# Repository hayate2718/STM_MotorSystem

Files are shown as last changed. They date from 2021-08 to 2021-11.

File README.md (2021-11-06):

# STM_MotorSystem
モーターシステム<br>
MCU_bord_subは半導体不足でMCP2562のSOIC8pinパッケージがなかったとき用<br>
VL逆接したら多分壊れるので気を付けてね。ダイオードつけるの忘れてたてへぺろリン<br>
ファームウェアなどプログラム関係は[STM_MotorSystem_Programのwiki](https://github.com/hayate2718/STM_MotorSystem_Program/wiki)を参照

|ピン|ペリフェラル|用途|
|---|---|---|
|PA0|TIM2(エンコーダモード)|直行エンコーダB相|
|PA1|TIM2(エンコーダモード)|直行エンコーダA相|
|PA2|GPIO(INPUT)|FF1|
|PA3|GPIO(INPUT)|FF2|
|PA5|ADC2|電流センサ出力|
|PA7|GPIO(OUTPUT)|RESET|
|PB0|TIM3(PWM)|モータ制御用PWM|
|PB1|GPIO(INPUT)|基板アドレス用ID1bit|
|PA8|GPIO(INPUT)|基板アドレス用ID2bit|
|PA9|GPIO(INPUT)|基板アドレス用ID3bit|
|PA10|GPIO(INPUT)|基板アドレス用ID4bit|
|PA11|CAN_RX|CAN_RX|
|PA12|CAN_TX|CAN_TX|
|PB4|GPIO(OUTPUT)|DIR|
|PB5|GPIO(OUTPUT)|COAST|

## 結局スナバ回路つけなかった

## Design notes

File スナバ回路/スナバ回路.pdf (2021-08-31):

# モータシステム：スナバ回路設計データ

### 小野澤颯

2021 年 8 月 30 日

## 1 目次

1. スナバ回路について
2. 非放電型スナバ回路の計算
3. モータシステム FET ブリッジへの実装
4. 参考文献

## 2 本編

1. スナバ回路について
MOSFET は非常に高速でスイッチングされるため、ドレイン電流は非常に急な変化をする。 例えば、モータ制御回路の H ブリッジ部に注目し、ハイサイド FET がターンオンしていると きモータに電流 I が流れる。次にターンオフしたとき、配線の寄生インダクタンス Lparasitic、 モータのインダクタンス成分 Lm によって、ドレインソース間には (Lparasitic + Lm)

dI
dt に従い、
大きなサージ電圧が発生する。このサージ電圧が FET の Vds(max) を超えると破壊される。

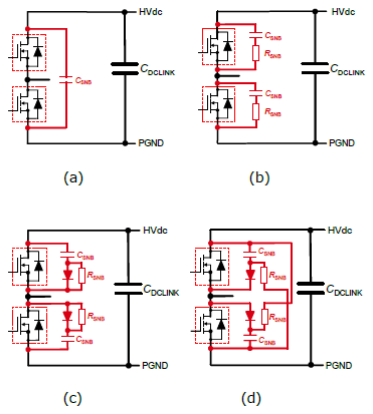
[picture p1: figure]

図 1: 各種スナバ回路

スナバ回路は破壊原因となる寄生成分によるサージを吸収し、FET の過渡電圧保護をする保 護回路の一種である。スナバ回路には大きく 4 種類あり、まず図１.(a) の C スナバ回路、次に 図 1.(b) に示す RC スナバ回路、図 1.(c) の RCD スナバ回路、図 1.(d) の非放電型 RCD スナバ 回路である。ここでは、非放電型 RCD スナバ回路を取り扱う。
非放電型 RCD スナバ回路は各種スナバ回路の中でもっともサージ吸収効果を高めることが 可能であり、スナバコンデンサがスイッチング毎に放電されないため、スナバ抵抗の消費電力 はサージによる電力のみとなる。したがって、スナバコンデンサの値を大きくすることができ るため、サージ吸収効果を大きく高めることが可能となる。他のスナバ回路ではスナバコンデ ンサがスイッチング毎に放電し、スナバ抵抗で電力を消費するため、スイッチング周波数が大 きくなると抵抗の消費電力が増大し、スナバコンデンサの大きさが制限される。他に比べ、非 放電型スナバ回路はメリットが多いが、もっとも配線レイアウトが複雑になるため、層の少な い基板では実装するのが困難である。
2. 非放電型 RCD スナバ回路の計算
非放電型 RCD スナバ回路の設計方法を示します。寄生インダクタンスにたまったエネルギー をスナバコンデンサで吸収することでサージを吸収しているため、スナバコンデンサは

Csnb >

LparasiticI

2

(Vds(surge) − Vsource)
2

(1)

で求める。これはインダクタンスのエネルギー式とコンデンサのエネルギー式から明らかであ る。
次に、吸収した電力の 90%を消費するスナバ抵抗の設計方法を示す。

Rsnb <

1

fswCsnb2.3

(2)

この抵抗器は、小さすぎると発振する可能性があるためできるだけ用件満たす範囲で多き値 を使う。
上式の求め方を下記に簡単に示す。前提として、Vc = Vsource(1 − e

− t
rc ) は RC 直列回路のコ
ンデンサ電位の t 軸関数である。

Vc(snb) = Vds(surge)(1 − e

− | t
RsnbCsnb ) | (3)

t はスイッチング周期だから　 t =

1
fsw

Vc(snb) = Vds(surge)(1 − e

− | 1
fswRsnbCsnb ) | (4)

e

− 1
fswRsnbCsnb =

Vds(surge) − Vc(snb)

Vds(surge)

(5)
−

1

fswRsnbCsnb

= log[

Vds(surge) − Vc(snb)

Vds(surge)

] | (6)

Rsnb =

−1

fswCsnblog[

Vds(surge)−Vc(snb)

Vds(surge)

]

(7)

コンデンサ電位を 90%消費するとき　 Vc(snb) = 0.9Vds(surge)

log[

Vds(surge) − 0.9Vds(surge)

Vds(surge)

] ≃ −2.3 | (8)

次に、スナバ抵抗の消費電力の設計方法を示す。

Psnb =

LparasiticI

2
fsw
2

(9)

これは、寄生インダクタンスのエネルギーがスイッチング毎に消費されていることを示して いる。

3. モータシステム FET ブリッジへの実装
用いるスナバ回路はまず、モータシステムで扱う最大電流 Imax、電源電圧 Vsource、FET の絶 対最大定格 Vmax、PWM 周波数 fsw を定義する。 例として、(あくまで例です（重要なことなので二回言います）)
Imax = 100[A] | (10)
Vsource = 24[V ] | (11)
Vmax = 30[V ] | (12)
fsw = 100[kHz] | (13)

と定義する。また、ここでは寄生インダクタンスを 100nH と定義する。
したがって、式 1 より、Csnb > 0.28[nF] となり、E 系列より 0.33[µF] を選択する。
式 2 より、Rsnb < 13[Ω] となるため、10[Ω] を選択する。
式 9 より、抵抗の損失は Psnb = 50[W] となるが、この電力は現実的ではないため、100A が 流れる時はモータの過渡電流と考え、約 0.1sec とし、半分の 5[W] 抵抗を用いる。（これでもで かいなぁ）
4. 参考文献
Rohm アプリケーションノート [スナバ回路の設計](62AN036J) (https://fscdn.rohm.com/jp/products/databook/applinote/discrete/sic/mosfet/sic-mos_snubber_circuit_design_an-j.pdf) 富士電機　アプリケーションノート [保護回路設計法] (https://www.fujielectric.co.jp/products/semiconductor/model/igbt/application/igbt.html)

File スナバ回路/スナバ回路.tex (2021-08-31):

\documentclass[12pt,a4paper,dvipdfmx]{jarticle}
\usepackage[top = 20truemm, bottom = 20truemm, left = 15truemm , right = 15truemm]{geometry}
\usepackage[dvipdfmx]{graphicx}
\usepackage{here}
\usepackage[dvipdfmx]{hyperref}
\usepackage{pxjahyper}
\hypersetup{
	bookmarksnumbered = true,
	colorlinks = true,
	setpagesize = false,
	linkcolor = blue,
	urlcolor = blue
}
\title{モータシステム：スナバ回路設計データ}
\author{小野澤颯}
\begin{document}
\maketitle
\section {目次}
\begin {enumerate}
	\item \hyperlink{section1}{スナバ回路について}
	\item \hyperlink{section2}{非放電型スナバ回路の計算}
	\item \hyperlink{section3}{モータシステムFETブリッジへの実装}
	\item \hyperlink{section4}{参考文献}
\end{enumerate}
\section {本編}
\begin{enumerate}
	\item \hypertarget{section1}{スナバ回路について}\\
		　MOSFETは非常に高速でスイッチングされるため、ドレイン電流は非常に急な変化をする。例えば、モータ制御回路のHブリッジ部に注目し、ハイサイドFETがターンオンしているときモータに電流$I$が流れる。次にターンオフしたとき、配線の寄生インダクタンス$L_{parasitic}$、モータのインダクタンス成分$L_{m}$によって、ドレインソース間には$(L_{parasitic}+L_{m})\frac{dI}{dt}$に従い、大きなサージ電圧が発生する。このサージ電圧がFETの$V_{ds(max)}$を超えると破壊される。\\
		\begin{figure}[H]
		\centering
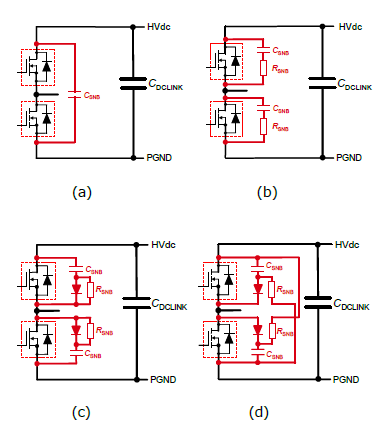
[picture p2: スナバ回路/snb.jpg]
		
		\caption{各種スナバ回路}
		\end{figure}
		　スナバ回路は破壊原因となる寄生成分によるサージを吸収し、FETの過渡電圧保護をする保護回路の一種である。スナバ回路には大きく4種類あり、まず図１.(a)のCスナバ回路、次に図1.(b)に示すRCスナバ回路、図1.(c)のRCDスナバ回路、図1.(d)の非放電型RCDスナバ回路である。ここでは、非放電型RCDスナバ回路を取り扱う。\\
		　非放電型RCDスナバ回路は各種スナバ回路の中でもっともサージ吸収効果を高めることが可能であり、スナバコンデンサがスイッチング毎に放電されないため、スナバ抵抗の消費電力はサージによる電力のみとなる。したがって、スナバコンデンサの値を大きくすることができるため、サージ吸収効果を大きく高めることが可能となる。他のスナバ回路ではスナバコンデンサがスイッチング毎に放電し、スナバ抵抗で電力を消費するため、スイッチング周波数が大きくなると抵抗の消費電力が増大し、スナバコンデンサの大きさが制限される。他に比べ、非放電型スナバ回路はメリットが多いが、もっとも配線レイアウトが複雑になるため、層の少ない基板では実装するのが困難である。
	\item \hypertarget{section2}{非放電型RCDスナバ回路の計算}\\
		 　非放電型RCDスナバ回路の設計方法を示します。寄生インダクタンスにたまったエネルギーをスナバコンデンサで吸収することでサージを吸収しているため、スナバコンデンサは
		 \begin{equation}
		 \label{csnb}
		 C_{snb}>\frac{L_{parasitic}I^2}{(V_{ds(surge)}-V_{source})^2}
		 \end{equation}
		で求める。これはインダクタンスのエネルギー式とコンデンサのエネルギー式から明らかである。\\
		　次に、吸収した電力の90\%を消費するスナバ抵抗の設計方法を示す。
		\begin{equation}
		\label{rsnb}
		R_{snb}<\frac{1}{f_{sw}C_{snb}2.3}
		\end{equation}
		　この抵抗器は、小さすぎると発振する可能性があるためできるだけ用件満たす範囲で多き値を使う。\\
		　上式の求め方を下記に簡単に示す。前提として、$V_c=V_{source}(1-e^{-\frac{t}{rc}})$はRC直列回路のコンデンサ電位のt軸関数である。
		\begin{eqnarray}
		V_{c(snb)}=V_{ds(surge)}(1-e^{-\frac{t}{R_{snb}C_{snb}}})
		\end{eqnarray}
		tはスイッチング周期だから　$t=\frac{1}{f_{sw}}$
		\begin{eqnarray}
		V_{c(snb)}=V_{ds(surge)}(1-e^{-\frac{1}{f_{sw}R_{snb}C_{snb}}})\\
		e^{-\frac{1}{f_{sw}R_{snb}C_{snb}}}=\frac{V_{ds(surge)}-V_{c(snb)}}{V_{ds(surge)}}\\
		-\frac{1}{f_{sw}R_{snb}C_{snb}}=log[\frac{V_{ds(surge)}-V_{c(snb)}}{V_{ds(surge)}}
]\\
		R_{snb}=\frac{-1}{f_{sw}C_{snb}log[\frac{V_{ds(surge)}-V_{c(snb)}}{V_{ds(surge)}}
]}
		\end{eqnarray}
		コンデンサ電位を90\%消費するとき　$V_{c(snb)}=0.9V_{ds(surge)}$\\
		\begin{eqnarray}
		log[\frac{V_{ds(surge)}-0.9V_{ds(surge)}}{V_{ds(surge)}}]\simeq-2.3
		\end{eqnarray}
		　次に、スナバ抵抗の消費電力の設計方法を示す。\\
		\begin{equation}
		\label{psnb}
		P_{snb}=\frac{L_{parasitic}I^2f_sw}{2}
		\end{equation}
		　これは、寄生インダクタンスのエネルギーがスイッチング毎に消費されていることを示している。\\
	\item \hypertarget{section3}{モータシステムFETブリッジへの実装}\\
		　用いるスナバ回路はまず、モータシステムで扱う最大電流$I_{max}$、電源電圧$V_{source}$、FETの絶対最大定格$V_{max}$、PWM周波数$f_{sw}$を定義する。\\
		　例として、(あくまで例です（重要なことなので二回言います）)
		\begin{eqnarray}
			I_{max} = 100 [A]\\
			V_{source} = 24 [V]\\
			V_{max} = 30 [V]\\
			f_{sw} = 100 [kHz]
		\end{eqnarray}
		と定義する。また、ここでは寄生インダクタンスを$100nH$と定義する。\\
		　したがって、式\ref{csnb}より、$C_{snb}　> 0.28 [nF]$となり、E系列より$0.33[\mu F]$を選択する。\\
		 　式\ref{rsnb}より、$R_{snb} < 13 [\Omega]$となるため、$10 [\Omega]$を選択する。\\
		 　式\ref{psnb}より、抵抗の損失は$P_{snb} = 50[W]$となるが、この電力は現実的ではないため、100Aが流れる時はモータの過渡電流と考え、約0.1secとし、半分の$5[W]$抵抗を用いる。（これでもでかいなぁ）
	\item \hypertarget{section4}{参考文献}\\
		Rohm　\href{https://fscdn.rohm.com/jp/products/databook/applinote/discrete/sic/mosfet/sic-mos_snubber_circuit_design_an-j.pdf}{アプリケーションノート[スナバ回路の設計](62AN036J)}\\
		富士電機　\href{https://www.fujielectric.co.jp/products/semiconductor/model/igbt/application/igbt.html}{アプリケーションノート[保護回路設計法]}
		
\end{enumerate}

\end{document}

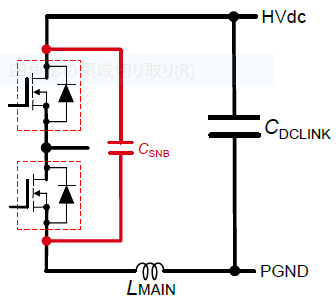
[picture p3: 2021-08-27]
スナバ回路/csnb.jpg

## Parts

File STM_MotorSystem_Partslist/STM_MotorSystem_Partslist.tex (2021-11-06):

\documentclass[12pt,a4paper,dvipdfmx]{jarticle}
\usepackage[top = 20truemm, bottom = 20truemm, left = 15truemm , right = 15truemm]{geometry}
\usepackage[dvipdfmx]{graphicx}
\usepackage{here}
\usepackage[dvipdfmx]{hyperref}
\usepackage{pxjahyper}
\hypersetup{
	bookmarksnumbered = true,
	colorlinks = true,
	setpagesize = false,
	linkcolor = blue,
	urlcolor = blue
}
\title{STMMotorSystemパーツリスト}
\author{小野澤颯}
\begin{document}
\maketitle
\begin{tabular}{ccccl}
	\hline
	部品名 &必要個数& 買う場所 & 金額 & 備考\\
	\hline
	XH8PIN &2& \href{hhttps://akizukidenshi.com/catalog/g/gC-12253/}{秋月電子} & 15 &コネクタ\\
	\hline
	XH5PIN$1$\href{https://akizukidenshi.com/catalog/g/gC-12250/}{秋月電子}$15$\\
	\hline
	JQ8PIN$2$\href{https://www.digikey.jp/product-detail/ja/jst-sales-america-inc/08JQ-BT/455-2970-ND/4918702}{digikey}$67$現在品切れ\\
	\hline
	VL4PIN&1&\href{https://www.digikey.jp/product-detail/ja/jst-sales-america-inc/B04P-VL-VN-1-8/455-3601-ND/2426345}{digikey}&156 &現在品切れ\\
	\hline
	box10pinL&1&\href{https://akizukidenshi.com/catalog/g/gC-13178/}{秋月電子}&25&ライトアングルタイプ\\
	\hline
	BOX14P$1$\href{https://www.digikey.jp/product-detail/ja/samtec-inc/FTSH-107-01-L-D-K/612-FTSH-107-01-L-D-K-ND/6693516}{digikey}$574$1.27ピッチ\\
	\hline
	TAKUTOSUITTI2$1$\href{https://akizukidenshi.com/catalog/g/gP-14888/}{秋月電子}$110$5個入り\\
	\hline
	DIPSW4$1$\href{https://akizukidenshi.com/catalog/g/gP-08929/}{秋月電子}$100$\\
	\hline
	ADP151AUJZ &1&\href{https://akizukidenshi.com/catalog/g/gI-14180/}{秋月電子}&90&\\
	\hline
	NJW1616T&1&\href{https://akizukidenshi.com/catalog/g/gI-15765/}{秋月電子}&90&\\
	\hline
	TLP291&1&\href{https://akizukidenshi.com/catalog/g/gI-16070/}{秋月電子}&180&10個入り\\
	\hline
	TLP293-4&1&\href{https://akizukidenshi.com/catalog/g/gI-16115/}{秋月電子}&80&\\
	\hline
	TLP152&1&\href{https://akizukidenshi.com/catalog/g/gI-10824/}{秋月電子}&80&\\
	\hline
	A3921&1&\href{https://akizukidenshi.com/catalog/g/gI-12293/}{秋月電子}&350&\\
	\hline
	ACS711&1&\href{https://akizukidenshi.com/catalog/g/gI-12267/}{秋月電子}&240&デフォではこいつ使おうとしてた\\
	\hline
	MCP2562$1$\href{https://www.digikey.jp/product-detail/ja/microchip-technology/MCP2562T-E-SN/MCP2562T-E-SNCT-ND/5011025}{digikey}$134$SOIC8PIN、現在在庫なし\\
	\hline
	STM32F303K$1$\href{https://akizukidenshi.com/catalog/g/gI-10790/}{秋月電子}$500$\\
	\hline
	SBR15U30SP5&4&\href{https://akizukidenshi.com/catalog/g/gI-07391/}{秋月電子}&50&\\
	\hline
	SS2040&1&\href{https://akizukidenshi.com/catalog/g/gI-02073/}{秋月電子}&300&20個入り\\
	\hline
	SKI03021&4&\href{https://akizukidenshi.com/catalog/g/gI-08473/}{秋月電子}&100&\\
	\hline
	FDC6305&2&\href{https://akizukidenshi.com/catalog/g/gI-06003/}{秋月電子}&120&10個入り\\
	\hline
	RGBLED&1&\href{https://akizukidenshi.com/catalog/g/gI-12726/}{秋月電子}&100&10個入り\\
	\hline
	0Ω&1& & &1608\\
	\hline
	1kΩ&5& & &1608\\
	\hline
	2.4kΩ&1& & &1608\\
	\hline
	20kΩ&1& & &1608\\
	\hline
	33kΩ&1& & &1608\\
	\hline
	10kΩ&7& & &1608\\
	\hline
	10Ω&5& & &1608\\
	\hline
	3.3kΩ&1& & &1608\\
	\hline
	2kΩ&1& & &1608\\
	\hline
	120Ω$1$$$1608\\
	\hline
	集合10k&2&\href{https://akizukidenshi.com/catalog/g/gP-04664/}{秋月電子}&100&1005、100個入り\\
	\hline
	集合1k&3&\href{https://www.mouser.jp/ProductDetail/667-EXB-38V102JV}{Mouser}&12&0603\\
	\hline
	330uF&3&\href{https://akizukidenshi.com/catalog/g/gP-14450/}{秋月電子}&80&\\
	\hline
	0.1uF&7& & &1608\\
	\hline
	1uF&2& & &1608\\
	\hline
	0.22uF&2& & &1608\\
	\hline
	10uF&1& & &1608\\
	\hline
	4.7uF&1& & &1608\\
	\hline
	2.2uF&2& & &1608\\
	\hline
	100uF&1& & &3216\\
	\hline
	22uH&1&\href{https://akizukidenshi.com/catalog/g/gP-08321/}{秋月電子}&60&\\
	\hline
	CSTN12MHz$1$\href{https://akizukidenshi.com/catalog/g/gP-14561/}{秋月電子}$110$5個入り、セラロック\\
	\hline
\end{tabular}

\end{document}

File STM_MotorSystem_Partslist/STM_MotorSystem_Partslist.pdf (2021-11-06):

# STMMotorSystemパーツリスト

## 小野澤颯

### 2021 年 11 月 6 日

1

部品名 | 必要個数 買う場所 金額 備考
XH8PIN | 2 | 秋月電子 | 15 | コネクタ
XH5PIN1 秋月電子 (https://akizukidenshi.com/catalog/g/gC-12250/) 15
JQ8PIN2digikey67 (https://www.digikey.jp/product-detail/ja/jst-sales-america-inc/08JQ-BT/455-2970-ND/4918702) 現在品切れ
VL4PIN | 1 | digikey (https://www.digikey.jp/product-detail/ja/jst-sales-america-inc/B04P-VL-VN-1-8/455-3601-ND/2426345) | 156 | 現在品切れ
box10pinL | 1 | 秋月電子 (https://akizukidenshi.com/catalog/g/gC-13178/) | 25 | ライトアングルタイプ
BOX14P1digikey5741.27 (https://www.digikey.jp/product-detail/ja/samtec-inc/FTSH-107-01-L-D-K/612-FTSH-107-01-L-D-K-ND/6693516) ピッチ
TAKUTOSUITTI21 秋月電子 (https://akizukidenshi.com/catalog/g/gP-14888/) 1105 個入り DIPSW41 秋月電子 (https://akizukidenshi.com/catalog/g/gP-08929/) 100
ADP151AUJZ | 1 | 秋月電子 (https://akizukidenshi.com/catalog/g/gI-14180/) | 90
NJW1616T | 1 | 秋月電子 (https://akizukidenshi.com/catalog/g/gI-15765/) | 90
TLP291 | 1 | 秋月電子 (https://akizukidenshi.com/catalog/g/gI-16070/) | 180 | 10 個入り
TLP293-4 | 1 | 秋月電子 (https://akizukidenshi.com/catalog/g/gI-16115/) | 80
TLP152 | 1 | 秋月電子 (https://akizukidenshi.com/catalog/g/gI-10824/) | 80
A3921 | 1 | 秋月電子 (https://akizukidenshi.com/catalog/g/gI-12293/) | 350
ACS711 | 1 | 秋月電子 (https://akizukidenshi.com/catalog/g/gI-12267/) | 240 | デフォではこいつ使おうとしてた
MCP25621digikey134SOIC8PIN、現在在庫なし (https://www.digikey.jp/product-detail/ja/microchip-technology/MCP2562T-E-SN/MCP2562T-E-SNCT-ND/5011025) STM32F303K1 秋月電子 (https://akizukidenshi.com/catalog/g/gI-10790/) 500
SBR15U30SP5 | 4 | 秋月電子 (https://akizukidenshi.com/catalog/g/gI-07391/) | 50
SS2040 | 1 | 秋月電子 (https://akizukidenshi.com/catalog/g/gI-02073/) | 300 | 20 個入り
SKI03021 | 4 | 秋月電子 (https://akizukidenshi.com/catalog/g/gI-08473/) | 100
FDC6305 | 2 | 秋月電子 (https://akizukidenshi.com/catalog/g/gI-06003/) | 120 | 10 個入り
RGBLED | 1 | 秋月電子 (https://akizukidenshi.com/catalog/g/gI-12726/) | 100 | 10 個入り
0 Ω | 1 | | | 1608
1k Ω | 5 | | | 1608
2.4k Ω | 1 | | | 1608
20k Ω | 1 | | | 1608
33k Ω | 1 | | | 1608
10k Ω | 7 | | | 1608
10 Ω | 5 | | | 1608
3.3k Ω | 1 | | | 1608
2k Ω | 1 | | | 1608
120 Ω 11608
集合 10k | 2 | 秋月電子 (https://akizukidenshi.com/catalog/g/gP-04664/) | 100 | 1005、100 個入り
集合 1k | 3 | Mouser (https://www.mouser.jp/ProductDetail/667-EXB-38V102JV) | 12 | 0603
330uF | 3 | 秋月電子 (https://akizukidenshi.com/catalog/g/gP-14450/) | 80
0.1uF | 7 | | | 1608
1uF | 2 | | | 1608
0.22uF | 2 | | | 1608
10uF | 1 | | | 1608
4.7uF | 1 | | | 1608
2.2uF | 2 | | | 1608
100uF | 1 | | | 3216
22uH | 1 | 秋月電子 (https://akizukidenshi.com/catalog/g/gP-08321/) | 60
CSTN12MHz1 秋月電子 (https://akizukidenshi.com/catalog/g/gP-14561/) 1105 個入り、セラロック2

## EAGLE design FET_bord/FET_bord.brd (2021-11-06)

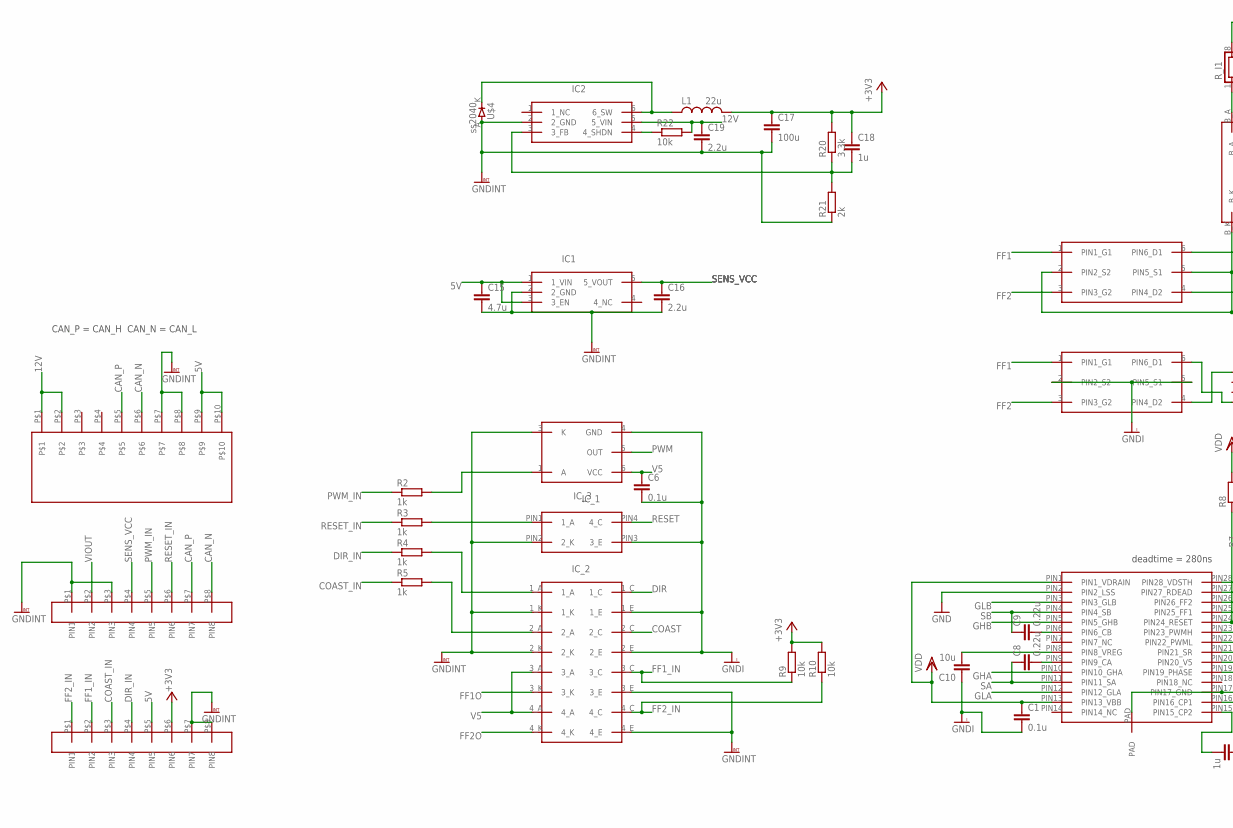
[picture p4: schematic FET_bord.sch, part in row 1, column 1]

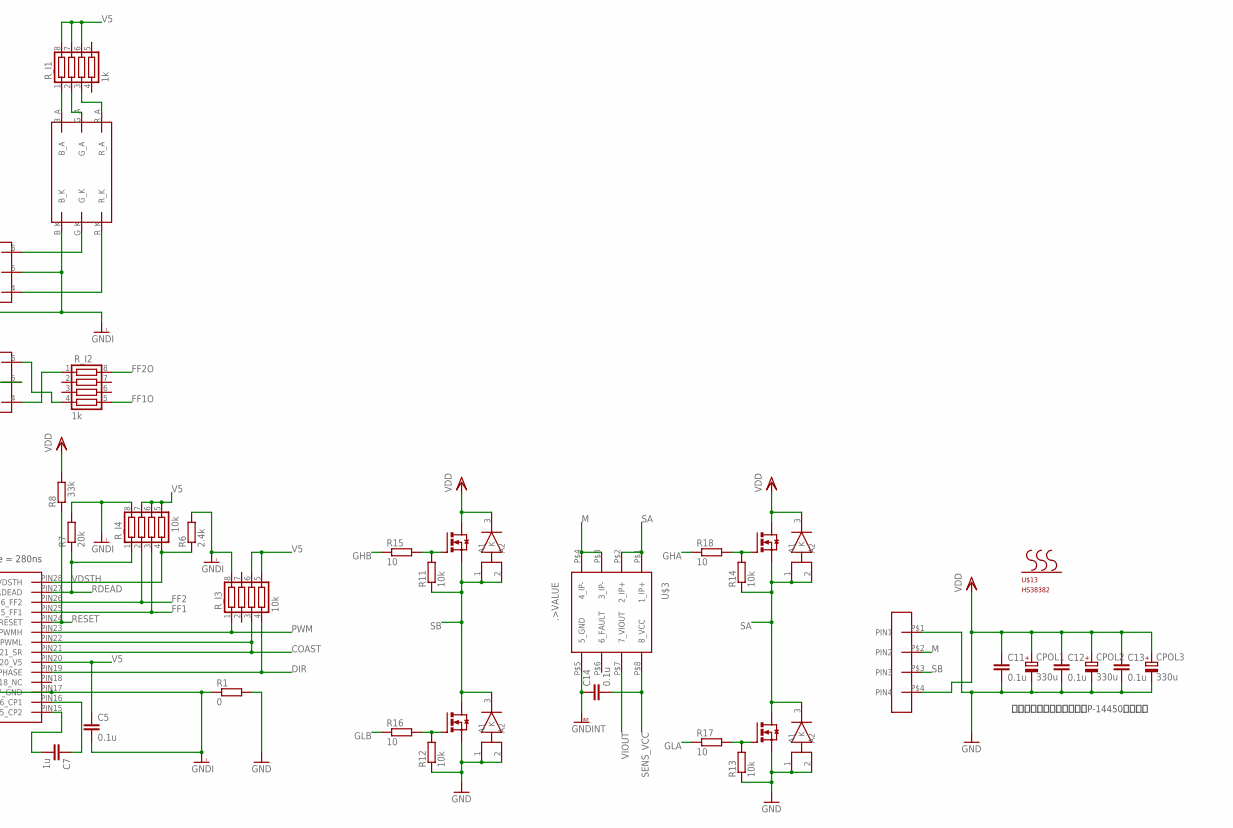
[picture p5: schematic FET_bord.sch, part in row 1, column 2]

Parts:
C1, C5, C6, C11, C12, C13, C14: 0.1u; C1608
C7, C18: 1u; C1608
C8, C9: 0.22u; C1608
C10: 10u; C1608
C15: 4.7u; C1608
C16, C19: 2.2u; C1608
C17: 100u; C3216
CON1, CON2: JQ_P8P
CPOL1, CPOL2, CPOL3: 330u; 1014CAPA
IC1: ADP151AUJZ; SOT23-5
IC2: NJW1616T; SOT23-6
IC_1: TLP291
IC_2: TLP290-4; TLP290
IC_3: TLP152; SO6-5
L1: 22u; SMD_INDUCTOR
R1: 0; 1608
R2, R3, R4, R5: 1k; 1608
R6: 2.4k; 1608
R7: 20k; 1608
R8: 33k; 1608
R9, R10, R11, R12, R13, R14, R22: 10k; 1608
R15, R16, R17, R18: 10; 1608
R20: 3.3k; 1608
R21: 2k; 1608
R_I1, R_I2: 1k; 0603X4RESISTOR
R_I3, R_I4: 10k; 1005X4RESISTOR
TR1, TR2, TR3, TR4: SKI03021; D2PACK
U$1: VL_4P
U$2: A3921; TSSOP_28P_ALLEGRO
U$3: ACS711; SOIC8
U$4: ss2040; SOD_123
U$5, U$7: FDC6305; SSOT6
U$6: RGB_LED
U$8: BOX10PBOX10P-L; BOX10P-L
U$9, U$10, U$11, U$12: SBR15U30SP5; POWERDI_5
U$13: HS38382; 38X38SQ

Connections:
5V: C15.1, CON1.P$5 (PIN5), IC1.1 (1_VIN), IC1.3 (3_EN), U$8.P$9, U$8.P$10
12V: C19.1, IC2.5 (5_VIN), R22.2, U$8.P$1, U$8.P$2
+3V3: C17.1, C18.1, CON1.P$6 (PIN6), L1.P$2 (2), R9.2, R10.2, R20.2
CAN_N: CON2.P$8 (PIN8), U$8.P$6
CAN_P: CON2.P$7 (PIN7), U$8.P$5
COAST: IC_2.2_C, R_I3.3, U$2.PIN21 (PIN21_SR), U$2.PIN22 (PIN22_PWML)
COAST_IN: CON1.P$3 (PIN3), R5.1
DIR: IC_2.1_C, R_I3.4, U$2.PIN19 (PIN19_PHASE)
DIR_IN: CON1.P$4 (PIN4), R4.1
FF1: R_I4.3, U$2.PIN25 (PIN25_FF1), U$5.1 (PIN1_G1), U$7.1 (PIN1_G1)
FF1O: IC_2.3_K, R_I2.5
FF1_IN: CON1.P$2 (PIN2), IC_2.3_C, R9.1
FF2: R_I4.2, U$2.PIN26 (PIN26_FF2), U$5.3 (PIN3_G2), U$7.3 (PIN3_G2)
FF2O: IC_2.4_K, R_I2.8
FF2_IN: CON1.P$1 (PIN1), IC_2.4_C, R10.1
GHA: R18.1, U$2.PIN10 (PIN10_GHA)
GHB: R15.1, U$2.PIN5 (PIN5_GHB)
GLA: R17.1, U$2.PIN12 (PIN12_GLA)
GLB: R16.1, U$2.PIN3 (PIN3_GLB)
GND: C11.2, C12.2, C13.2, CPOL1.-, CPOL2.-, CPOL3.-, R1.2, R12.1, R13.1, TR3.3 (PIN3_S), TR4.3 (PIN3_S), U$1.P$1 (PIN1), U$2.PIN2 (PIN2_LSS), U$10.1 (A1), U$10.2 (A2), U$11.1 (A1), U$11.2 (A2)
GNDI: C1.2, C5.2, C6.2, C10.1, IC_1.PIN3 (3_E), IC_2.1_E, IC_2.2_E, IC_3.4 (GND), R1.1, R6.2, R7.2, R_I3.8, R_I4.8, U$2.PAD, U$2.PIN17 (PIN17_GND), U$5.2 (PIN2_S2), U$5.5 (PIN5_S1), U$6.B_K, U$7.2 (PIN2_S2), U$7.5 (PIN5_S1)
GNDINT: C14.1, C15.2, C16.2, C17.2, C19.2, CON1.P$7 (PIN7), CON1.P$8 (PIN8), CON2.P$1 (PIN1), CON2.P$3 (PIN3), IC1.2 (2_GND), IC2.2 (2_GND), IC_1.PIN2 (2_K), IC_2.1_K, IC_2.2_K, IC_2.3_E, IC_2.4_E, IC_3.3 (K), R21.1, U$3.P$5 (5_GND), U$4.A, U$8.P$7, U$8.P$8
M: U$1.P$2 (PIN2), U$3.P$3 (3_IP-), U$3.P$4 (4_IP-)
unnamed: U$5.6 (PIN6_D1), U$6.G_K
unnamed: IC2.6 (6_SW), L1.P$1 (1), U$4.K (C)
unnamed: R_I2.1, U$7.4 (PIN4_D2)
unnamed: U$5.4 (PIN4_D2), U$6.R_K
unnamed: R_I1.1, U$6.B_A
unnamed: R_I1.2, U$6.G_A
unnamed: R_I1.3, U$6.R_A
unnamed: R_I2.4, U$7.6 (PIN6_D1)
unnamed: IC_3.1 (A), R2.2
unnamed: IC_1.PIN1 (1_A), R3.2
unnamed: IC_2.1_A, R4.2
unnamed: IC_2.2_A, R5.2
unnamed: C7.1, U$2.PIN16 (PIN16_CP1)
unnamed: C7.2, U$2.PIN15 (PIN15_CP2)
unnamed: C8.2, U$2.PIN9 (PIN9_CA)
unnamed: C9.2, U$2.PIN6 (PIN6_CB)
unnamed: C10.2, U$2.PIN8 (PIN8_VREG)
unnamed: C18.2, IC2.3 (3_FB), R20.1, R21.2
unnamed: R13.2, R17.2, TR4.1 (PIN1_G)
unnamed: R14.2, R18.2, TR2.1 (PIN1_G)
unnamed: R11.2, R15.2, TR1.1 (PIN1_G)
unnamed: R12.2, R16.2, TR3.1 (PIN1_G)
unnamed: IC2.4 (4_SHDN), R22.1
PWM: IC_3.5 (OUT), R_I3.1, U$2.PIN23 (PIN23_PWMH)
PWM_IN: CON2.P$5 (PIN5), R2.1
RDEAD: R7.1, R_I4.1, U$2.PIN27 (PIN27_RDEAD)
RESET: IC_1.PIN4 (4_C), R8.1, U$2.PIN24 (PIN24_RESET)
RESET_IN: CON2.P$6 (PIN6), R3.1
SA: C8.1, R14.1, TR2.3 (PIN3_S), TR4.2 (PIN2_D), U$2.PIN11 (PIN11_SA), U$3.P$1 (1_IP+), U$3.P$2 (2_IP+), U$11.3 (K), U$12.1 (A1), U$12.2 (A2)
SB: C9.1, R11.1, TR1.3 (PIN3_S), TR3.2 (PIN2_D), U$1.P$3 (PIN3), U$2.PIN4 (PIN4_SB), U$9.1 (A1), U$9.2 (A2), U$10.3 (K)
SENS_VCC: C14.2, C16.1, CON2.P$4 (PIN4), IC1.5 (5_VOUT), U$3.P$8 (8_VCC)
V5: C5.1, C6.1, IC_2.3_A, IC_2.4_A, IC_3.6 (VCC), R_I1.6, R_I1.7, R_I1.8, R_I3.5, R_I3.6, R_I4.5, R_I4.6, R_I4.7, U$2.PIN20 (PIN20_V5)
VDD: C1.1, C11.1, C12.1, C13.1, CPOL1.+, CPOL2.+, CPOL3.+, R8.2, TR1.2 (PIN2_D), TR2.2 (PIN2_D), U$1.P$4 (PIN4), U$2.PIN1 (PIN1_VDRAIN), U$2.PIN13 (PIN13_VBB), U$9.3 (K), U$12.3 (K)
VDSTH: R6.1, R_I4.4, U$2.PIN28 (PIN28_VDSTH)
VIOUT: CON2.P$2 (PIN2), U$3.P$7 (7_VIOUT)

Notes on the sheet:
deadtime = 280ns
電解コンデンサには秋月のP-14450を用いる
CAN_P = CAN_H CAN_N = CAN_L

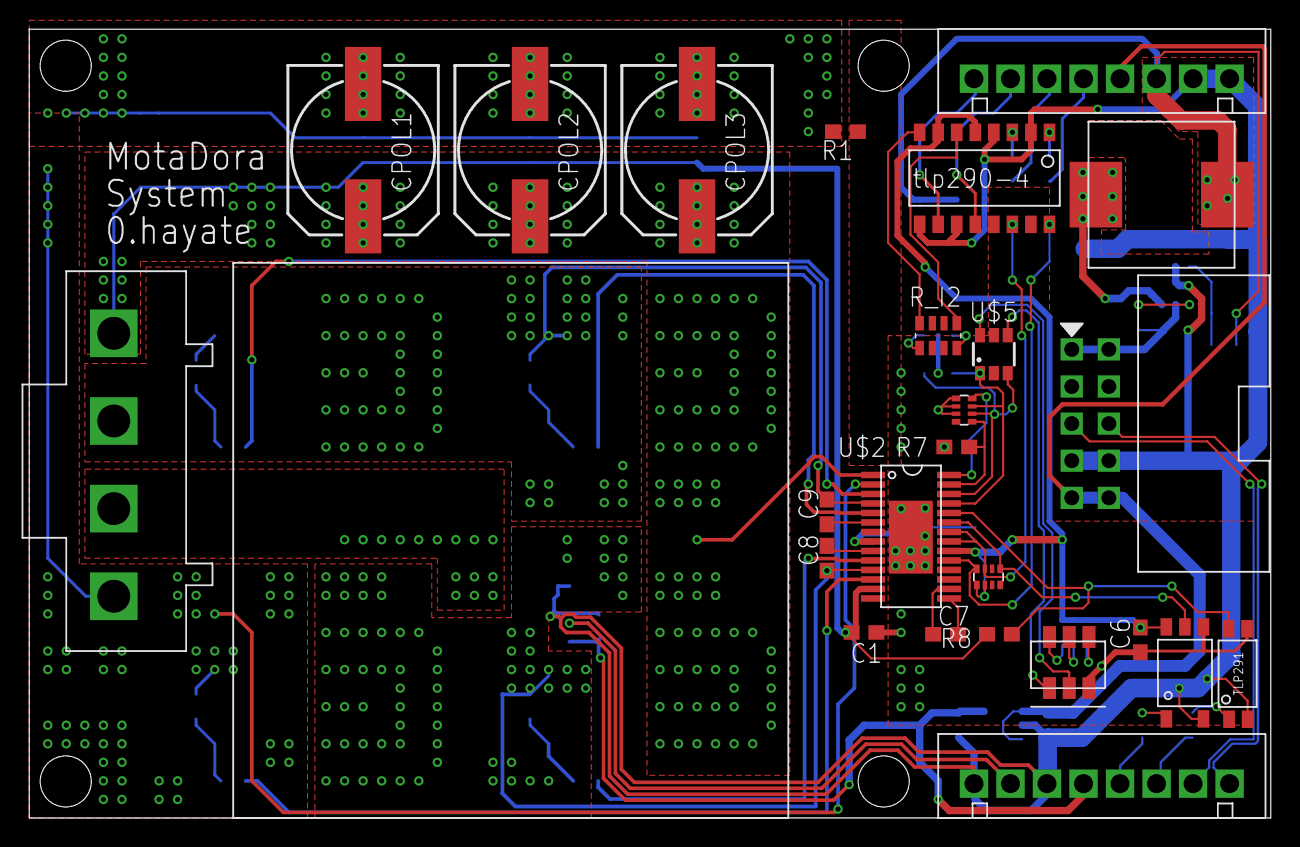
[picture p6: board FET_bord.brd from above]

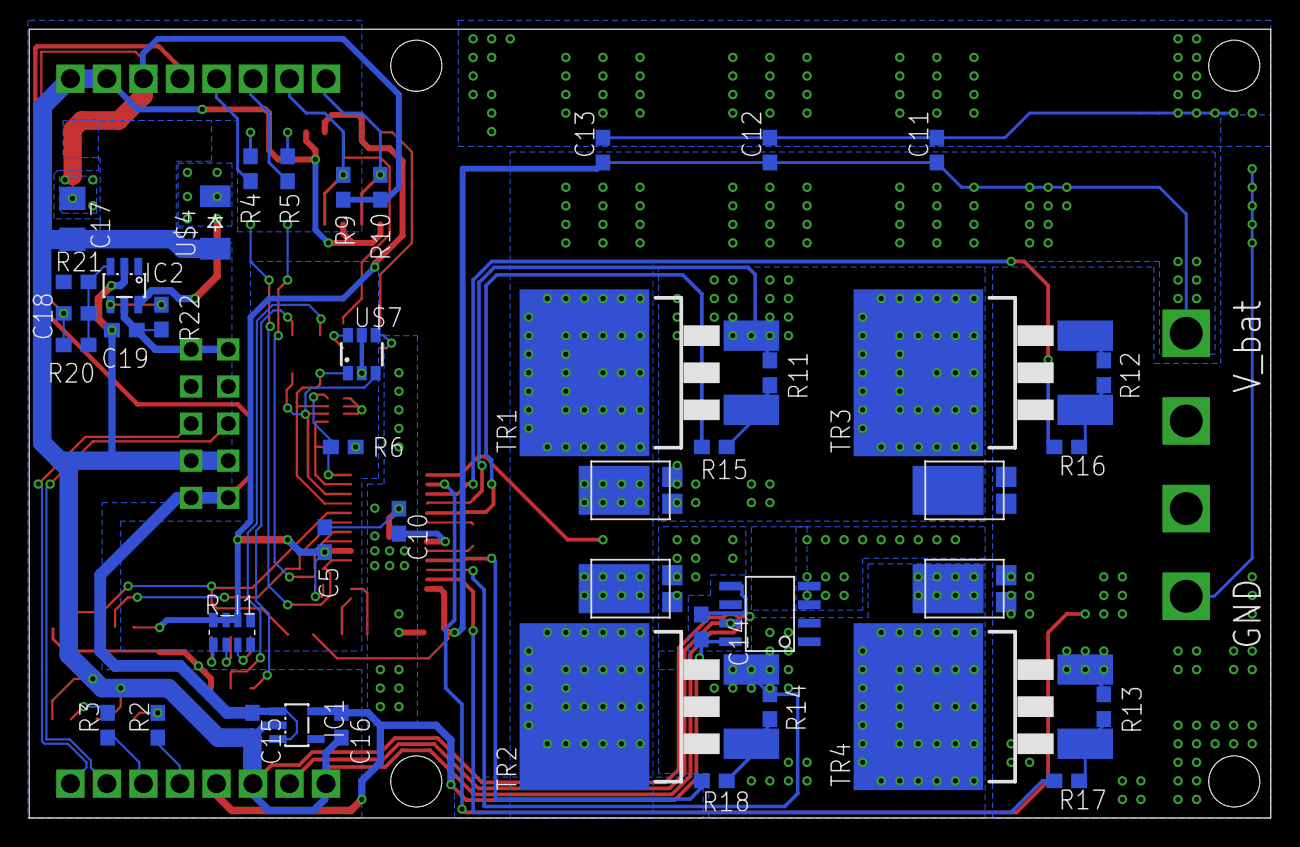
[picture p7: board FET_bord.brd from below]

Board: 2 copper layers, 85.0 x 54.0 mm, 69 parts (43 on the bottom side), 58 nets.

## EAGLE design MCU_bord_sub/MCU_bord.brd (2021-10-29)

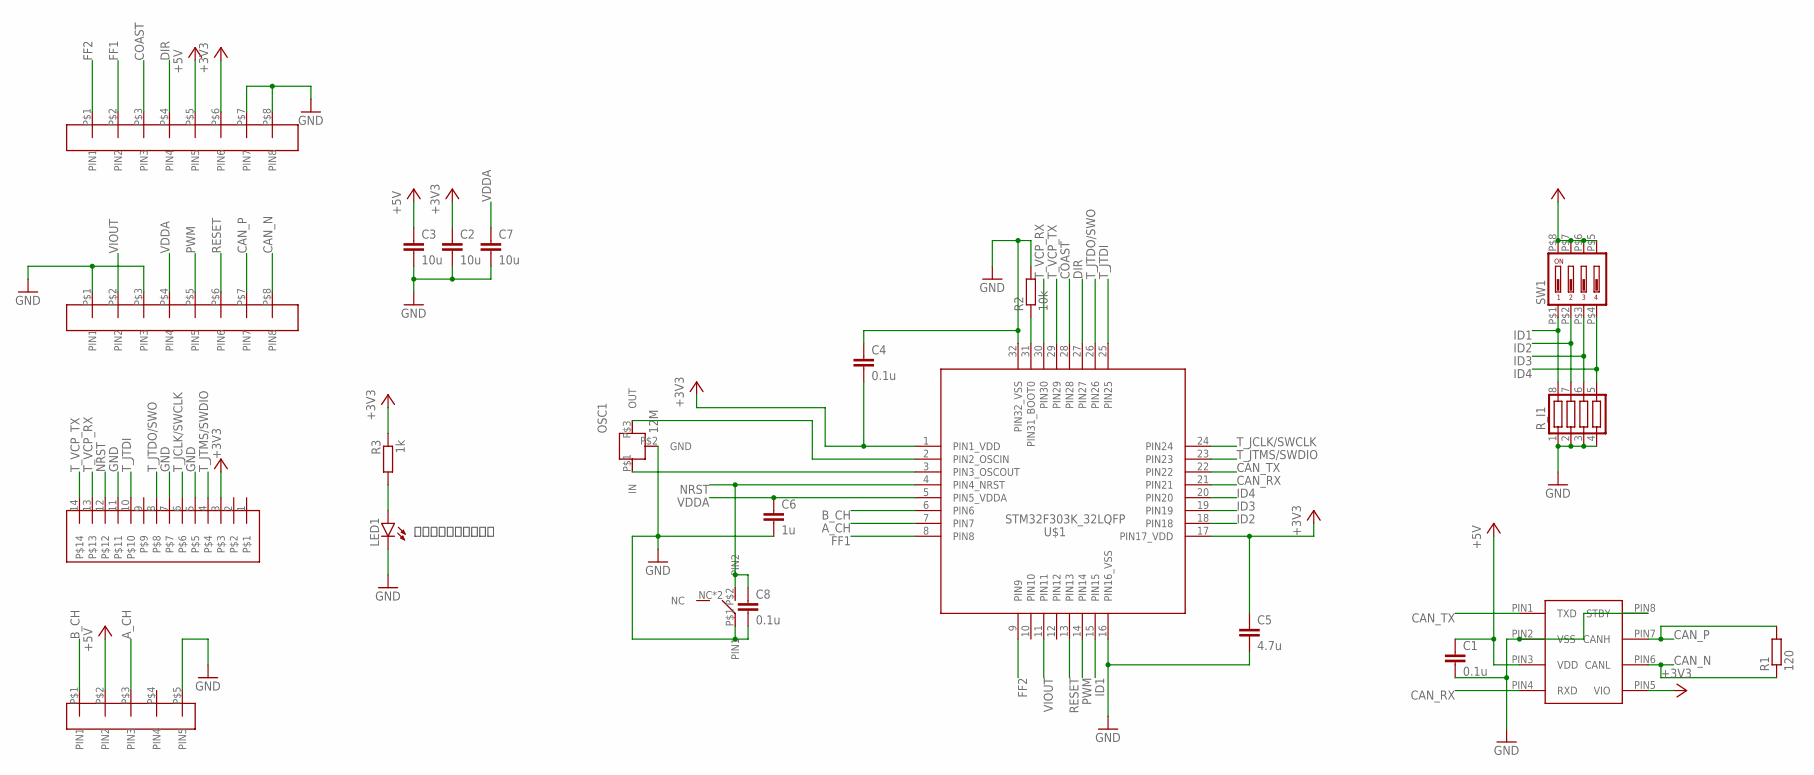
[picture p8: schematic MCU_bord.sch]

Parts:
C1, C4, C8: 0.1u; C1608
C2, C3, C7: 10u; C1608
C5: 4.7u; C1608
C6: 1u; C1608
CON1, CON2: JQ_S8P
CON3: XH_5P
IC1: MCP2562; DIL8
LED1: 1608LED; 1608
OSC1: 12M; CSTNE#
R1: 120; 1608
R2: 10k; 1608
R3: 1k; 1608
R_I1: R_SHUGOU2; 1005X4RESISTOR
SW1: DIPSW4
U$1: STM32F303K_32LQFP; LQFP32-7X7
U$2: TAKUTOSUITTI2
U$3: BOX14P; CON_HEDA14P_1.27

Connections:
+3V3: C2.1, C4.2, C5.1, CON1.P$6 (PIN6), IC1.PIN5 (VIO), R3.1, SW1.P$5 (5), SW1.P$6 (6), SW1.P$7 (7), SW1.P$8 (8), U$1.1 (PIN1_VDD), U$1.17 (PIN17_VDD), U$3.3
+5V: C1.1, C3.1, CON1.P$5 (PIN5), CON3.P$2 (PIN2), IC1.PIN3 (VDD)
A_CH: CON3.P$3 (PIN3), U$1.7 (PIN7)
B_CH: CON3.P$1 (PIN1), U$1.6 (PIN6)
CAN_N: CON2.P$8 (PIN8), IC1.PIN6 (CANL), R1.1
CAN_P: CON2.P$7 (PIN7), IC1.PIN7 (CANH), R1.2
CAN_RX: IC1.PIN4 (RXD), U$1.21 (PIN21)
CAN_TX: IC1.PIN1 (TXD), U$1.22 (PIN22)
COAST: CON1.P$3 (PIN3), U$1.28 (PIN28)
DIR: CON1.P$4 (PIN4), U$1.27 (PIN27)
FF1: CON1.P$2 (PIN2), U$1.8 (PIN8)
FF2: CON1.P$1 (PIN1), U$1.9 (PIN9)
GND: C1.2, C2.2, C3.2, C4.1, C5.2, C6.2, C7.2, C8.2, CON1.P$7 (PIN7), CON1.P$8 (PIN8), CON2.P$1 (PIN1), CON2.P$3 (PIN3), CON3.P$5 (PIN5), IC1.PIN2 (VSS), IC1.PIN8 (STBY), LED1.K, OSC1.P$2 (GND), R2.2, R_I1.1, R_I1.2, R_I1.3, R_I1.4, U$1.16 (PIN16_VSS), U$1.32 (PIN32_VSS), U$2.P$1 (PIN1), U$3.5, U$3.7, U$3.11
ID1: R_I1.8, SW1.P$1 (1), U$1.15 (PIN15)
ID2: R_I1.7, SW1.P$2 (2), U$1.18 (PIN18)
ID3: R_I1.6, SW1.P$3 (3), U$1.19 (PIN19)
ID4: R_I1.5, SW1.P$4 (4), U$1.20 (PIN20)
unnamed: OSC1.P$1 (IN), U$1.3 (PIN3_OSCOUT)
unnamed: OSC1.P$3 (OUT), U$1.2 (PIN2_OSCIN)
unnamed: R2.1, U$1.31 (PIN31_BOOT0)
unnamed: LED1.A, R3.2
NRST: C8.1, U$1.4 (PIN4_NRST), U$2.P$2 (PIN2), U$3.12
PWM: CON2.P$5 (PIN5), U$1.14 (PIN14)
RESET: CON2.P$6 (PIN6), U$1.13 (PIN13)
T_JCLK/SWCLK: U$1.24 (PIN24), U$3.6
T_JTDI: U$1.25 (PIN25), U$3.10
T_JTDO/SWO: U$1.26 (PIN26), U$3.8
T_JTMS/SWDIO: U$1.23 (PIN23), U$3.4
T_VCP_RX: U$1.30 (PIN30), U$3.13
T_VCP_TX: U$1.29 (PIN29), U$3.14
VDDA: C6.1, C7.1, CON2.P$4 (PIN4), U$1.5 (PIN5_VDDA)
VIOUT: CON2.P$2 (PIN2), U$1.11 (PIN11)

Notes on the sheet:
電源確認用色指定なし

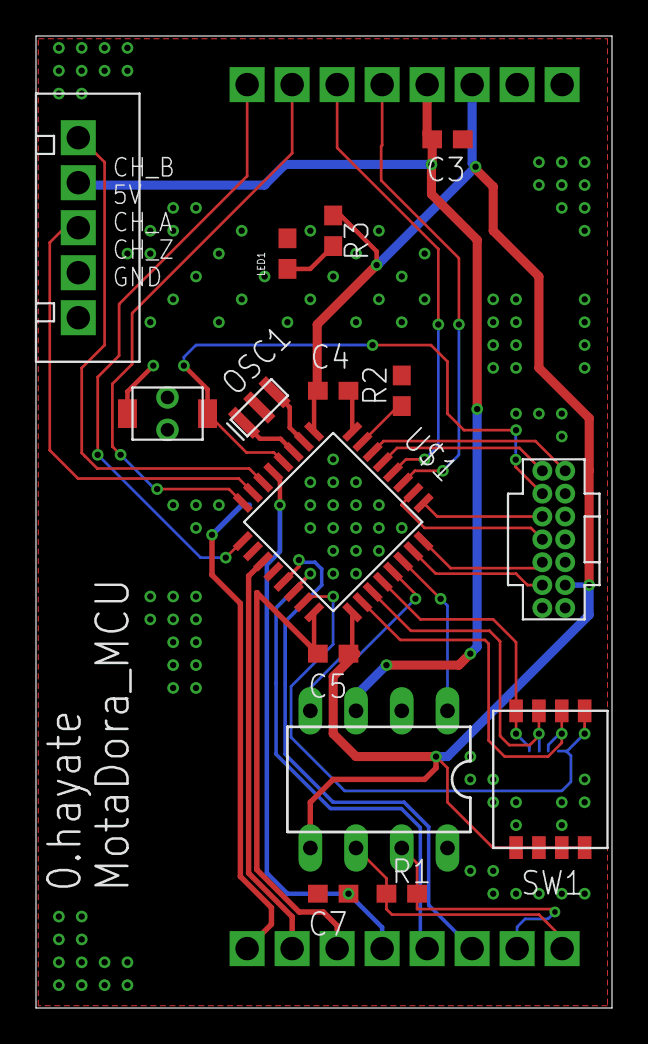
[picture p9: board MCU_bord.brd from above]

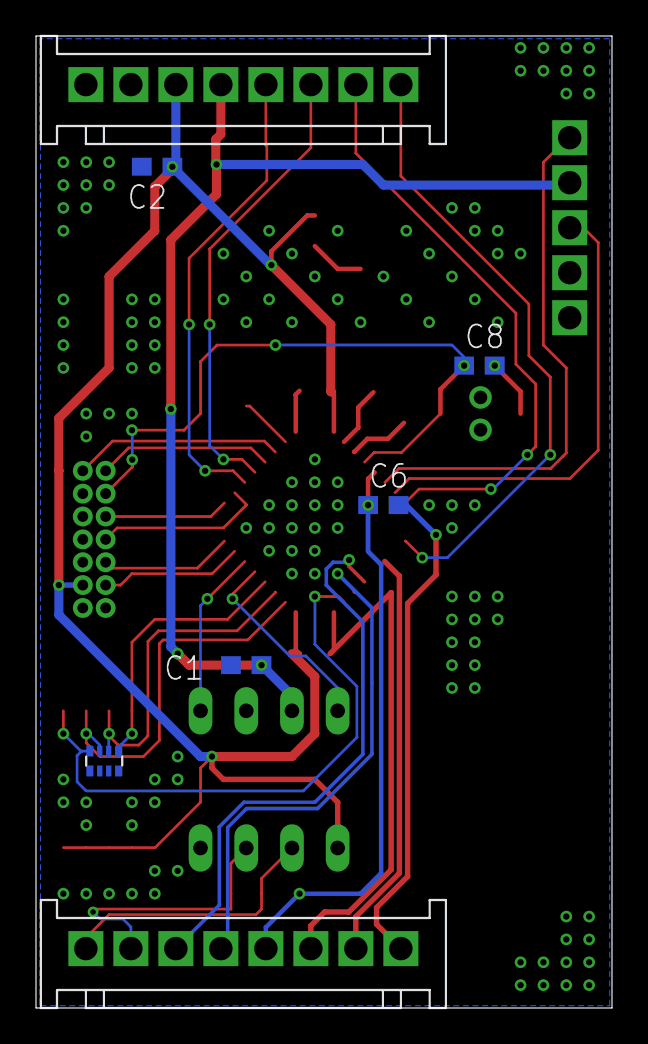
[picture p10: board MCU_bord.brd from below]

Board: 2 copper layers, 32.0 x 54.0 mm, 22 parts (7 on the bottom side), 32 nets.

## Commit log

2021-08-27 スナバ回路資料追加
    [FET_bord.brd, FET_bord.sch]
2021-08-27 記号修正
2021-08-27 スナバ追加
    [FET_bord.brd, FET_bord.sch]
2021-08-28 a3921ロジック回路周りの設計
    [FET_bord.brd, FET_bord.sch]
2021-08-30 ロジック部を設計
    [FET_bord.brd, FET_bord.sch]
2021-08-31 回路図ほぼ完成
    [FET_bord.brd, FET_bord.sch]
2021-08-31 基板設計を開始した
    [FET_bord.brd, FET_bord.sch]
2021-09-01 スナバ消した。基盤が結構仕上がってきた
    [FET_bord.brd, FET_bord.sch]
2021-09-01 基板設計ほぼ終わりあとは仕上げ
    [FET_bord.brd]
2021-09-02 設計終了、DRC通った。がばでたを出力した
    [FET_bord.brd]
2021-09-04 mcu側に着手
    [FET_bord.brd, FET_bord.sch, MCU_bord.brd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]
2021-09-05 mcu側回路図多分完成。基板側に着手する予定
    [MCU_bord.brd, MCU_bord.sch]
2021-09-05 MCU側完成。文字の位置とかの調整をやれば発注できる
    [MCU_bord.brd, MCU_bord.sch]
2021-09-05 TIMピンの選択ミスったのなおした
    [FET_bord.brd, MCU_bord.brd, MCU_bord.sch]
2021-09-05 ミス直し
    [MCU_bord.brd, MCU_bord.sch]
2021-09-13 端子名を記入
    [FET_bord.brd, MCU_bord.brd]
2021-09-14 発注用データ
    [ALL_bord.brd]
2021-09-14 がばでた
    [ALL_bord.brd]
2021-10-26 基板エラー修正
    [FET_bord.brd, FET_bord.sch, MCU_bord.brd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]
2021-10-28 canトランシーバ終端抵抗追加、電源確認用LED追加
    [MCU_bord.brd, MCU_bord.sch]
2021-10-29 DIL8PINverのMCP2562搭載MCUボード追加
    [MCU_bord.brd, MCU_bord.sch]
2021-11-06 集合抵抗value記入
    [FET_bord.brd, FET_bord.sch]
2021-11-06 ぱあつりすとついか
